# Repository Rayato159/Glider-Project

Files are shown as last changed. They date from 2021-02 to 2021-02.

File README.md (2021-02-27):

# Glider Project

 **Submitted by**
 1.	Ruangyot	Nanchiang	B6116736	(Project Manager)
 2.	Sahassawat	Rattanamongkolkul	B6113056	(CAD)
 3.	Kamonlaphat	Sitthitharanon	B6130268	(Documentation)
 4.	Apisit	Butprom	B6005375	(Manufacture)
 5.	Kobsiri	Seedakaew	B6007874	(Manufacture)
 6.	Chonlatorn	Sawangjit	B6007836	(Manufacture)
 
Present to Dr. Atthaphon Ariyarit.  
Semester 2-2563  
Suranaree University of Technology 

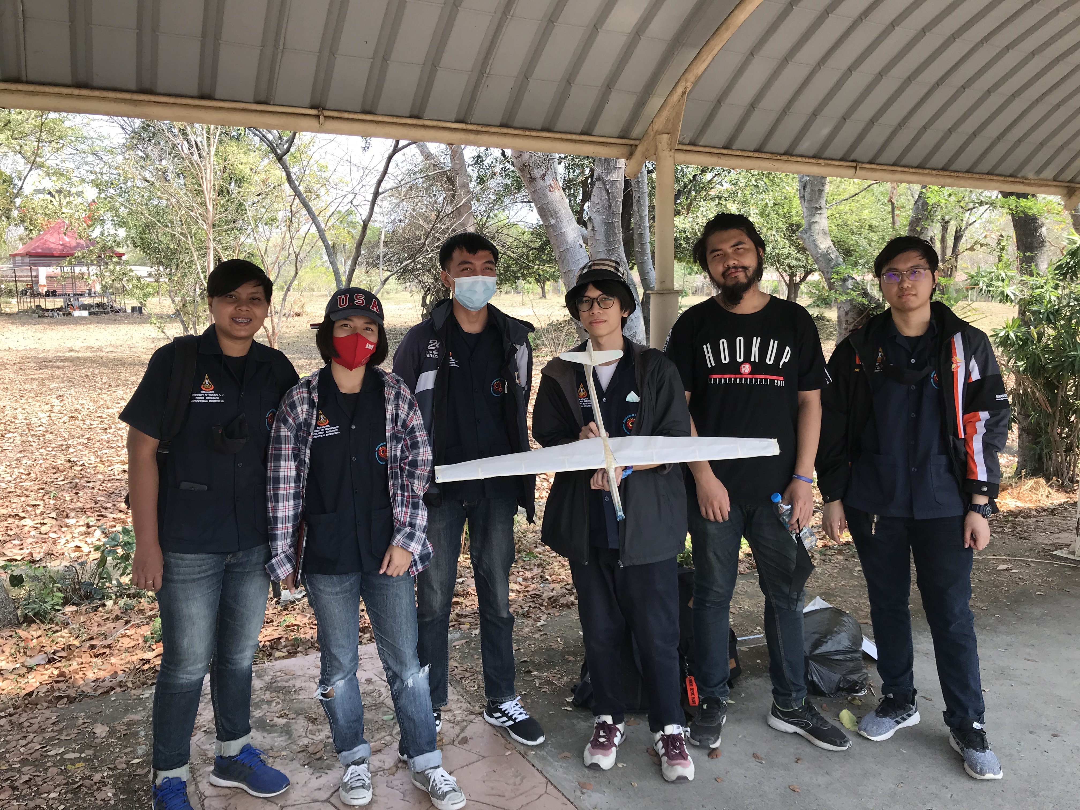
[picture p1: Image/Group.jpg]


This report is a part of the 537314 Flight Mechanics. The purpose of this report is to explain whole about of glider which we design whether why we need design like this.  
It’s just not only about to glider design but include manufacture, flight testing, inspection after flight testing and financial report.  
We describe step by step for who want to learn how to produce some small glider by our concept.  
This project is full of obstacles, because we just study the mechanics of flight and don’t know as much about aircraft design. Therefore, we used all the knowledge from aerodynamics and this subject by the full of power for produce the best glider as we can.  
Finally, If you read to this. We hope you to get the highest of knowledge by our report.  

Read more in full report.  
Flight Test: https://drive.google.com/drive/folders/1Cjw-I_sFbw1iagVFhjcJ2LFoMrj9WS8H?usp=sharing

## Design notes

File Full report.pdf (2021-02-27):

# Glider Project (Group No. 7)

537314 FLIGHT MECHANICS

### Submitted by

1. Ruangyot | Nanchiang | B6116736 (Project Manager)

### 2. Sahassawat Rattanamongkolkul B6113056 (CAD)

3. Kamonlaphat Sitthitharanon | B6130268 (Documentation)
4. Apisit | Butprom | B6005375 (Manufacture)
5. Kobsiri | Seedakaew | B6007874 (Manufacture)
6. Chonlatorn Sawangjit | B6007836 (Manufacture)
| | Present to

### Dr. Atthaphon Ariyarit

### Semester 2-2563

### Suranaree University of Technology

Preface
This report is a part of the 537314 Flight Mechanics. The purpose of this report is to explain whole about of glider which we design whether why we need design like this. It’s just not only about to glider design but include manufacture, flight testing, inspection after flight testing and financial report. We describe step by step for who want to learn how to produce some small glider by our concept.

This project is full of obstacles, because we just study the mechanics of flight and don’t know as much about aircraft design. Therefore, we used all the knowledge from aerodynamics and this subject by the full of power for produce the best glider as we can.

Finally, If you read to this. We hope you to get the highest of knowledge by our report.

Sincerely

project organizers

Contents

Glider Design Flowchart

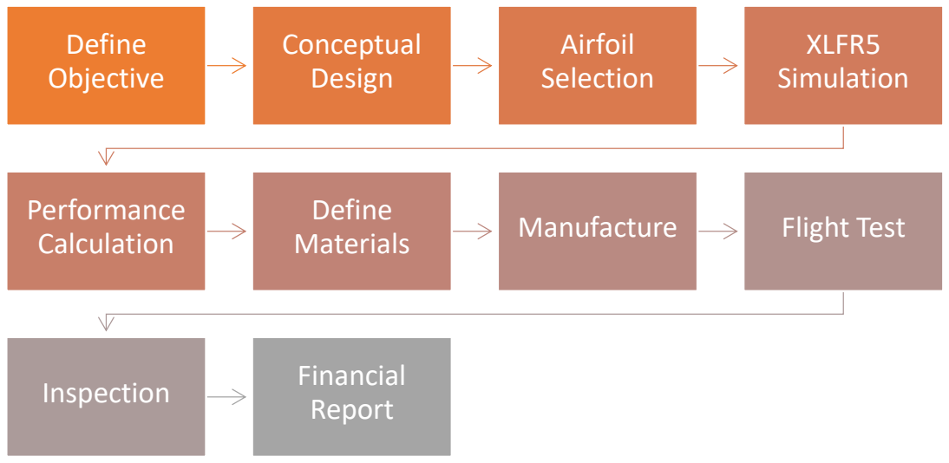
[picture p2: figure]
Define Objective; Conceptual Design; Airfoil Selection; XLFR5 Simulation; Performance Calculation; Define; Materials; Manufacture; Flight Test; Inspection; Financial; Report

Define Objective
1. Wingspan 1 m
2. Reynold number <= 400000 (Incompressible Flow)
3. Initial attitude 2 m
4. Longest range gliding
5. Low weight
6. High Cl/Cd and AR
7. High stiffness

Conceptual Design
The most important of glider is about to design for low weight, high Cl/Cd and AR, but in this project. We must design for high stiffness for structural test in another project.

First step. We need to define wing shape. From objective we need high Cl/Cd and AR then we define chord about 100 mm and we are all know as the best wing shape is elliptic wing (For lift produce on wing. Because elliptic wing has Oswald efficiency number = 1) But elliptic wing is hard to manufacture. Then taper wing is better to manufacture. Taper wing give speed more than rectangular wing for long range gliding. The good taper ratio are about 0.3 to 0.4. We choose taper ratio 0.4 and sweep angle 0 degree because is easy for manufacture. Then choose T tail for stable.

Next step. We used the RC plane calculator website to define all dimension and improve some dimension for suitability to structure.

Finally. We used Solidworks CAD software to design this glider, find center of gravity and calculate empty weight. Assume material to balsa wood.

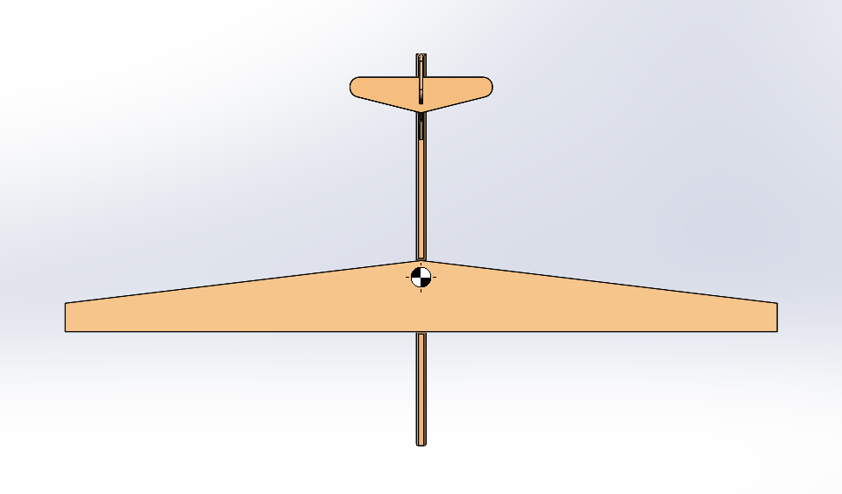
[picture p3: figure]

Figure 1 Top view

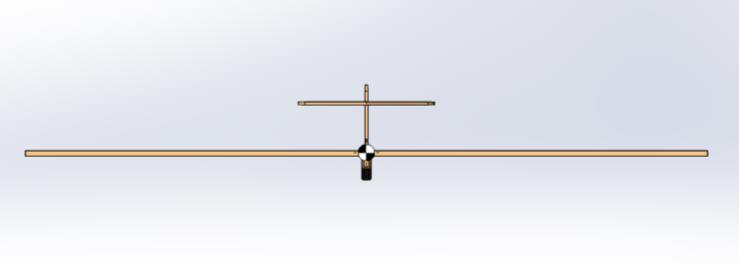
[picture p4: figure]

Figure 2 Front view

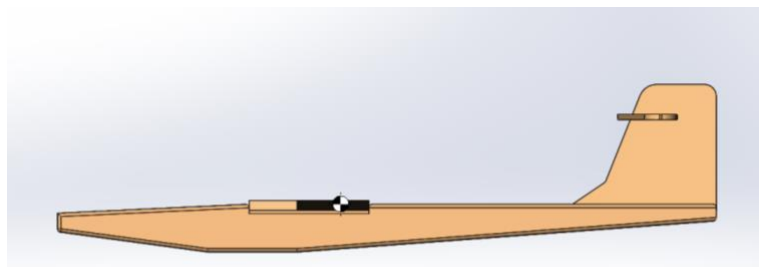
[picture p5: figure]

Figure 3 Right view

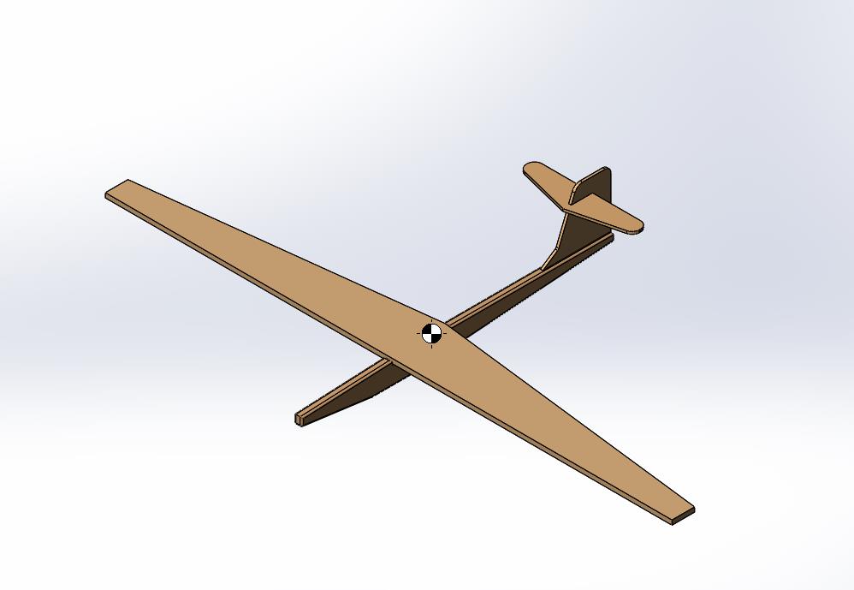
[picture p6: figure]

Figure 4 Isometric

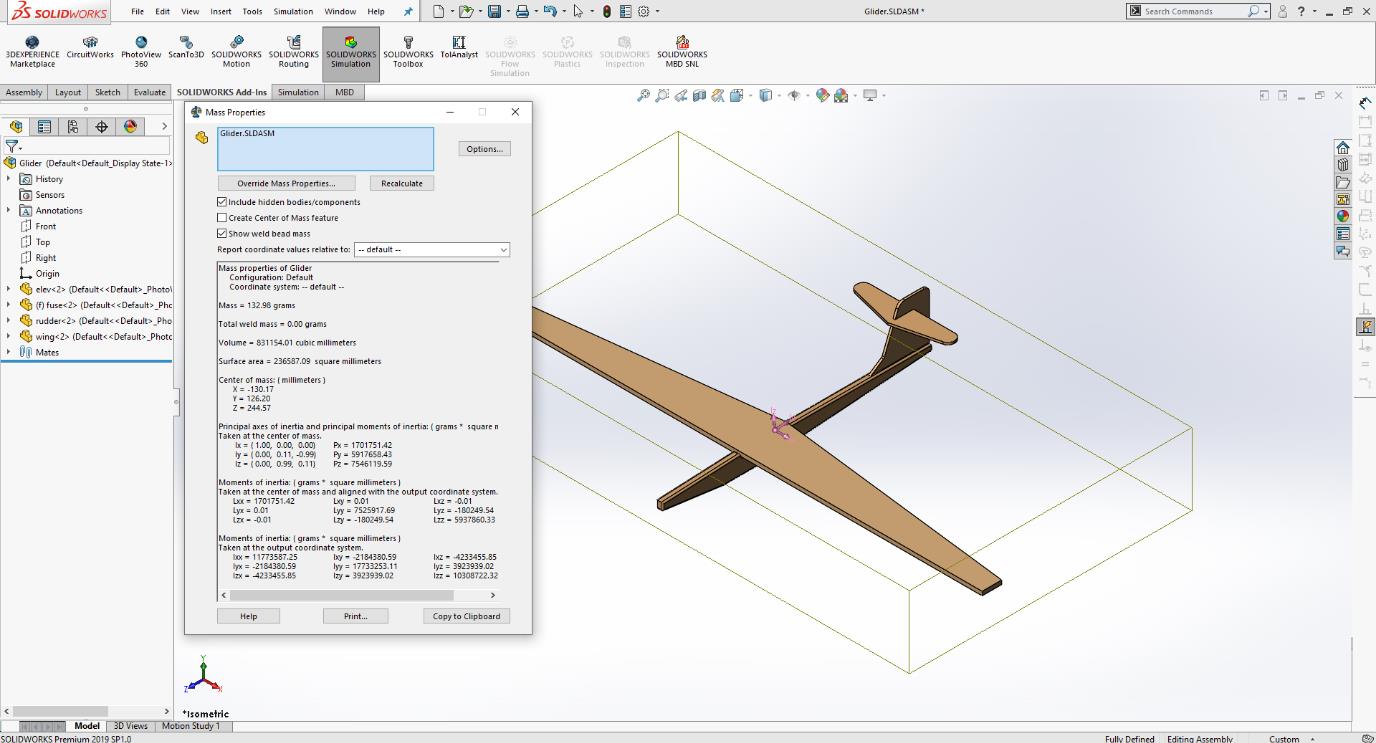
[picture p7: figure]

Figure 5 CG and mass calculation
Mass = 133 g; Center of Gravity (x, y, z) = (-130.17 mm, 126.20 mm, 244.57 mm);

Airfoils Selection
This step is also equally important, Because to improve Cl/Cd we need to meticulous with airfoil selection.

First step is about collection airfoils data. (We choose only NACA airfoils for standard) Go to “Airfoil Tools” website and collect all NACA airfoils coordinate point to JavaFoil. In JavaFoil set all

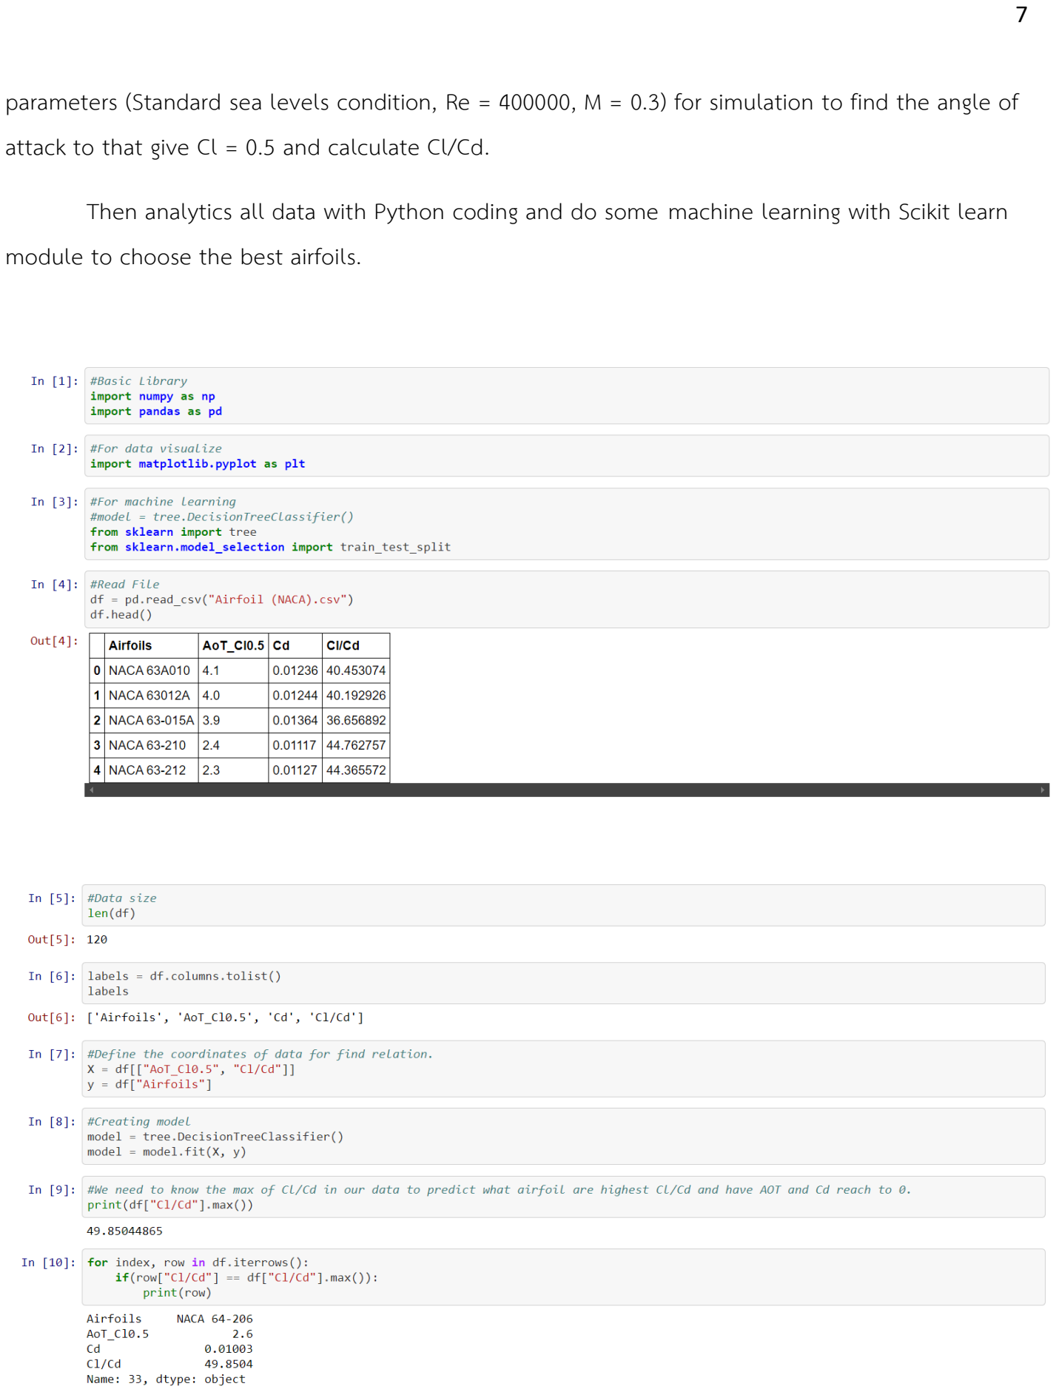
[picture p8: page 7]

parameters (Standard sea levels condition, Re = 400000, M = 0.3) for simulation to find the angle of attack to that give Cl = 0.5 and calculate Cl/Cd.

Then analytics all data with Python coding and do some machine learning with Scikit learn module to choose the best airfoils.

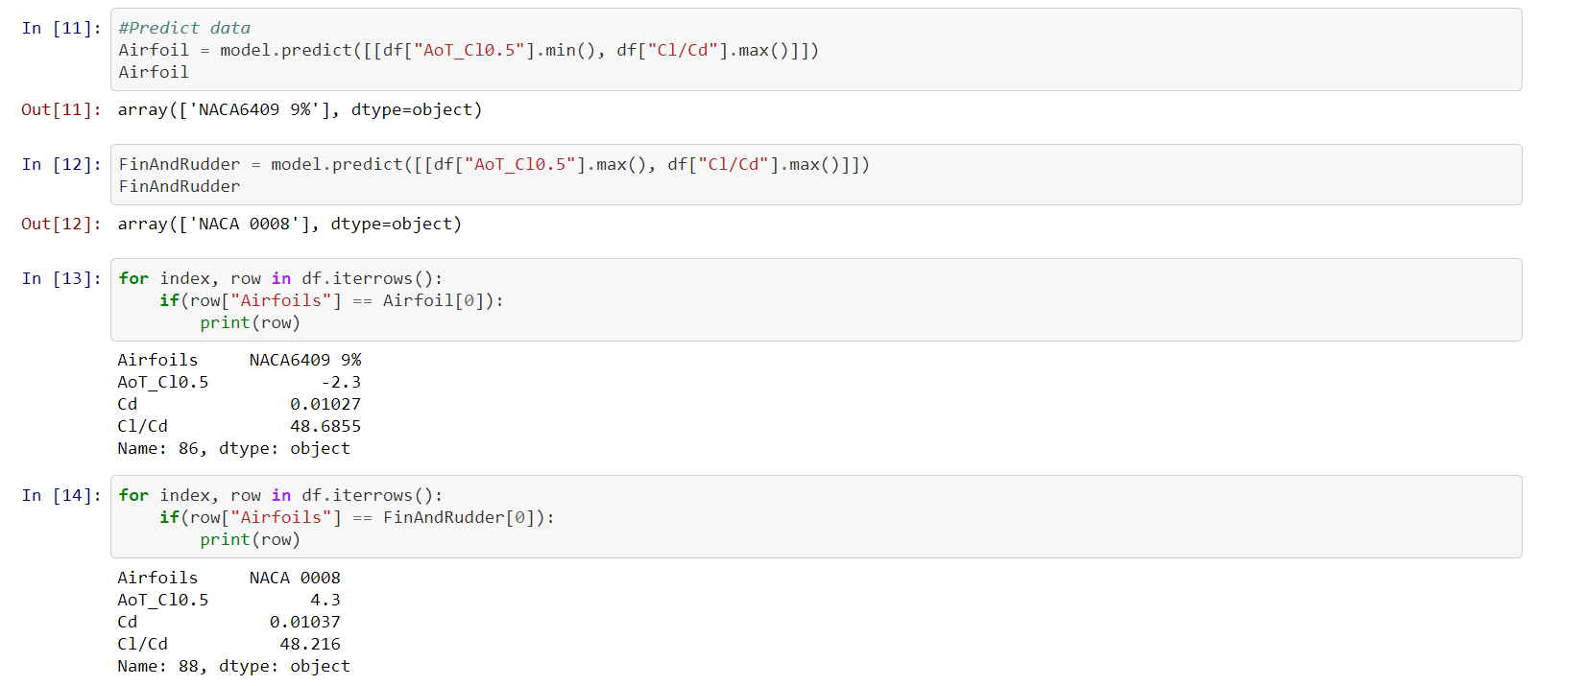
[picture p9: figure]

We used tree decision model because to define what if we need airfoil that have angle of attack and Cl/Cd by some value we expect. If wing we need lowest angle of attack and highest Cl/Cd for easy to launch the glider. If stabilizer we need symmetry airfoils and highest Cl/Cd for not disrupt the aerodynamics performance of the wing. what are airfoils we should get. And model score is 0.9833.

Thus, the result is NACA6409 for wing and NACA0008 for stabilizer (But used flat plate for tail because it’s can’t produce in reality for us).

XFLR5 Simulation
XFLR5 is free software and easy to use for RC plane simulation. This software can analysis airfoils and analysis RC plane. Then pull all information from conceptual design for define boundary conditions and get result below. Assume V = 9 m/s.

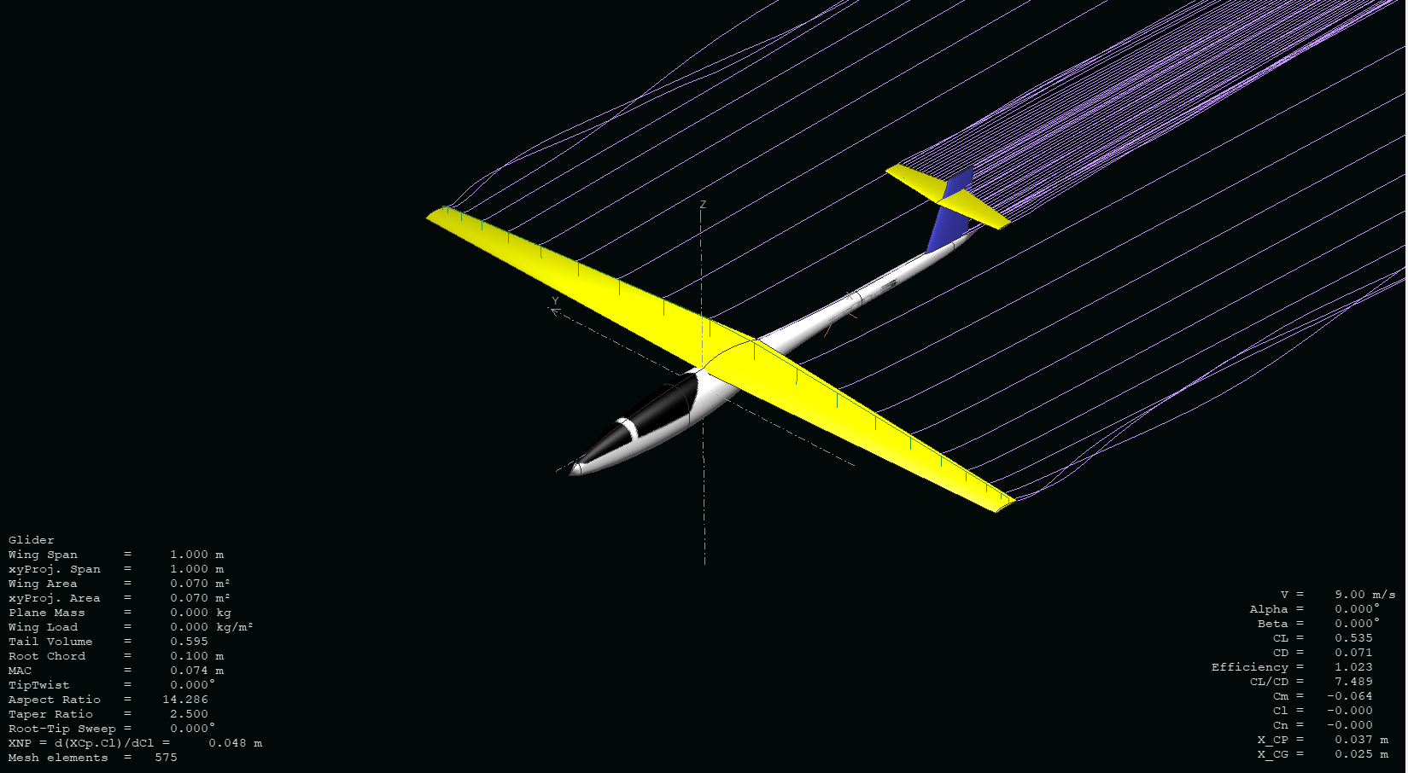
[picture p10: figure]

Figure 6 Streamline

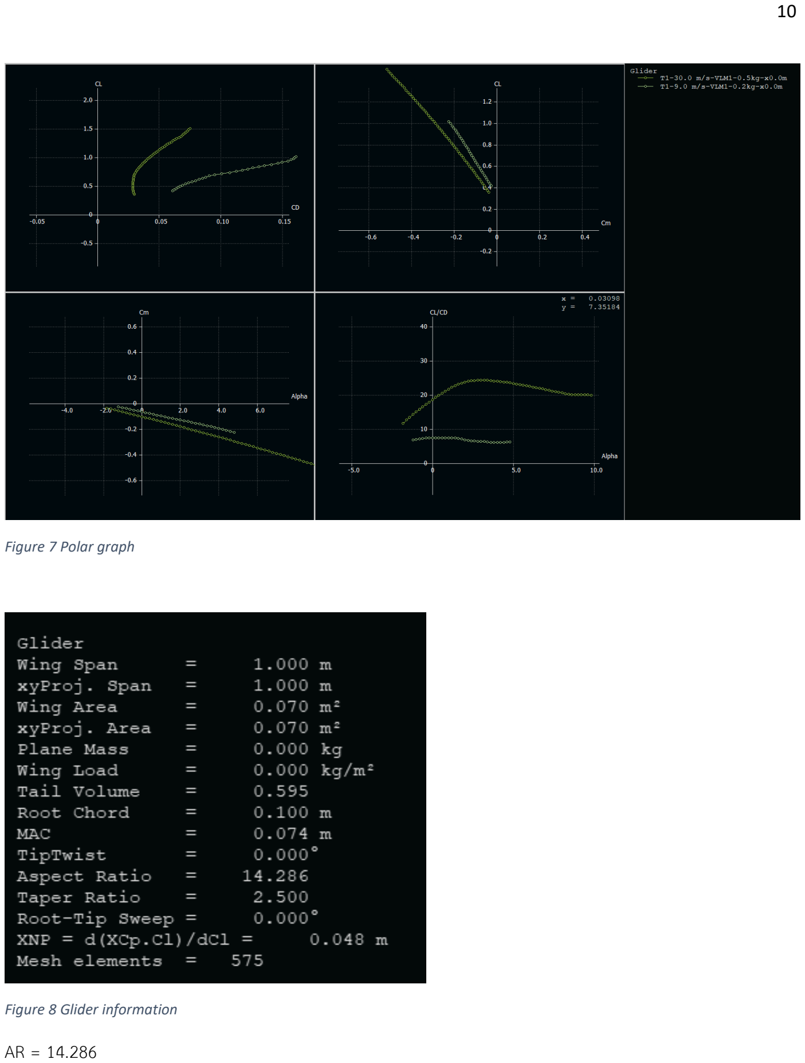
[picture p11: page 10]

Figure 7 Polar graph

Figure 8 Glider information
AR = 14.286

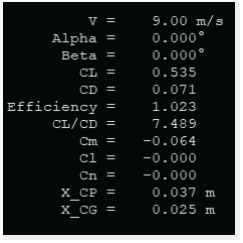
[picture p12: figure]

Figure 9 Glider performance
By plane analysis at angle of attack = 0 deg, Cl/Cd = 7.489, Cm = -0.064;

Performance Calculation
Consider an airplane in power off flight. The force acting on glider are lift, drag and weight. Thrust is zero because power off glider. Assume glider is constant velocity and flight path is horizontal parallel with ground. (L = W; T = D;)

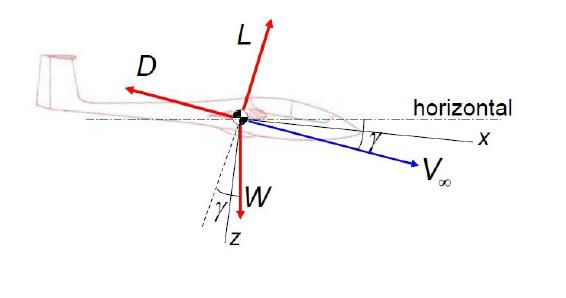
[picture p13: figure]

By the free body diagram is clearly whether if less of theta then range of glider will increase. If we want to know how far of glider can gliding. By following.

tan γ =

1
Cl
Cd

From that formula. Calculate gliding distance.

Cl
Cd = Glide Ratio = 7.489

tan γ =

1
7.489 = 0.134

Maximum range. h = 2 m

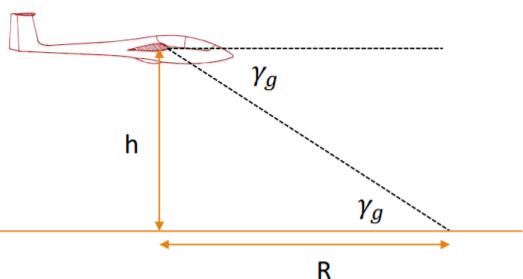
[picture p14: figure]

R =

h
tan γ

=

2
0.134 = 14.925 m

γ = tan⁻¹
(0.134) = 7.63 deg

Sink rate.

Sink rate =

Air Speed
Glide Ratio =

9
7.489 = 1.2 m/s

Endurance.

E =

h
Sink rate

=

2
1.2

= 1.67 sec

Thrust required.

TR =

W
Cl
Cd

=

0.133 ∗ 9.81
0.134 = 9.74 N ≈ 1 kg

Define Materials
At the first on conceptual Design. We assume all aircraft is filled by Balsa wood because Balsa wood is easy for manufacture, low cost and low weight. But in reality we can’t do that because we need to care about structure. Then we need to do some composite materials for more stiffness. And finally following the table below.
Materials | Part
Balsa Wood + PE Foam | Fuselage and Stabilizer
Balsa wood + Carbon Fiber | Wings
Kite Paper 50 gram | Wings Skin

***Carbon fiber spar has low weight and can improve stiffness for wings in vertical and axial load.

Manufacture
This process is full of obstacles. Because We have tools and resources in finite. We need to take carefully when we do all the parts by part of aircraft. We do “Handmade Workshop”.

Step by step

1. Fuselage: Cut the balsa wood and PE foam then stick together then fillet.
2. Stabilizer: Cut PE foam for 2 pieces first is vertical stabilizer second is horizontal stabilizer. Then cut some stick of balsa wood and stick together finally stick all to fuselage.
3. Airfoils: Cut come balsa wood and rasp to airfoils shape we select in first (7 pieces).
4. Wings: Used 2 carbon stick for wings spar and stick together with airfoils the cut some balsa wood to do bones of wings.
5. Wings Skin: Attach kite paper to wings.
6. Finally Step: Attach wing with fuselage by tape.

To more clarify whether how to manufacture.

Tools | Materials
Cutter | Balsa Wood, PE Foam
Rasp | Balsa Wood, PE Foam

Tools | Manufacture
Glue | Stick all the materials together
Tape | Attach wings to fuselage
Plasticine | Attach to glider for more weight and balance
Measured Tools | Used when
Vernier Caliper | Measured thickness
T Ruler | Check vertical or horizontal
Tape measure | Measured long range
Scales | Measured weight

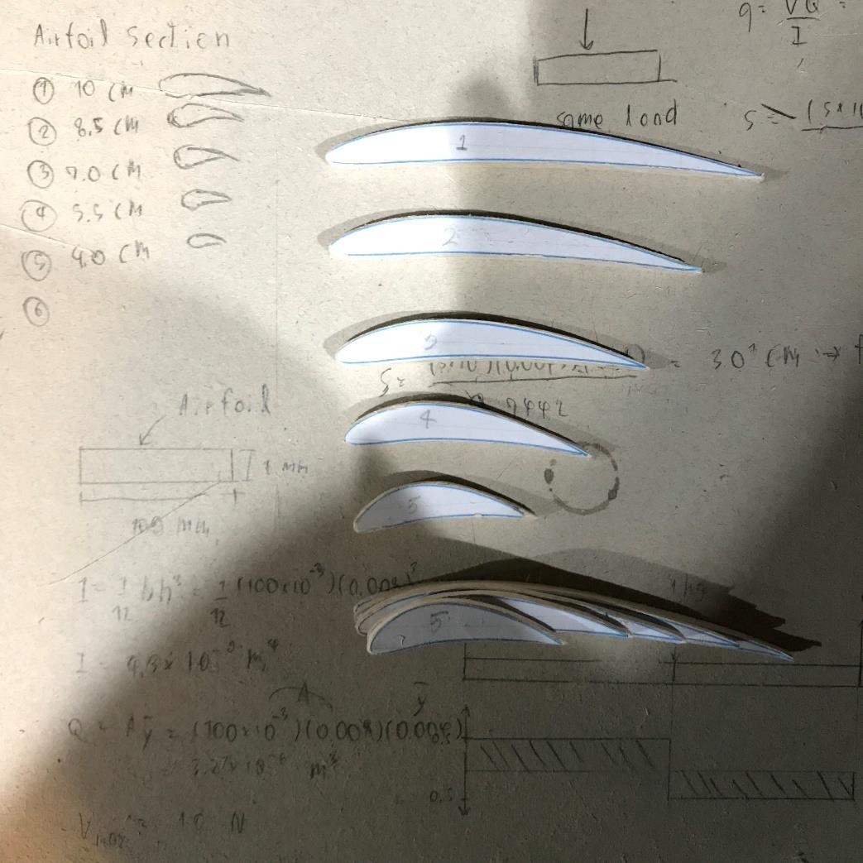
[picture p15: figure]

Figure 10 Airfoils NACA6409

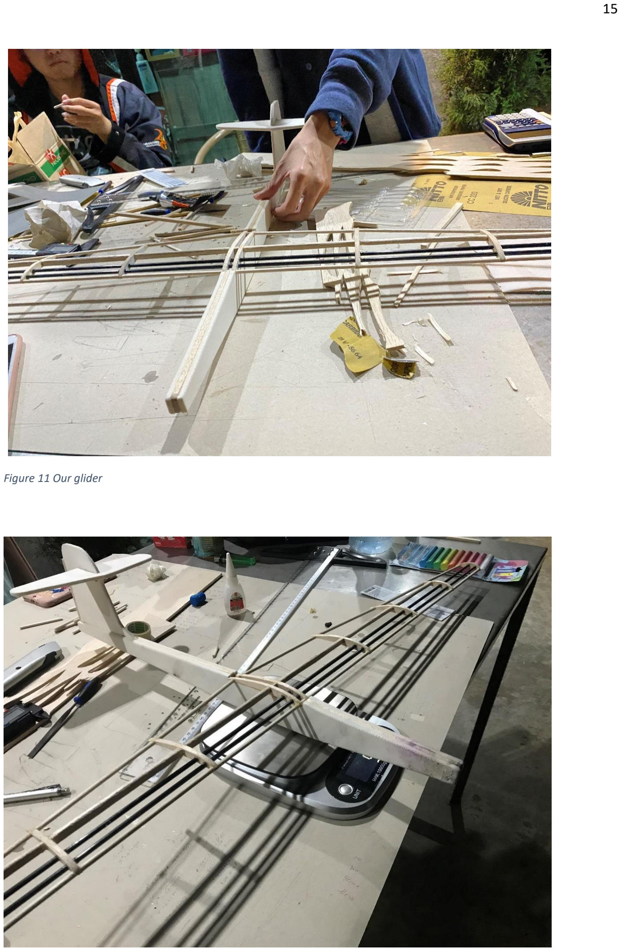
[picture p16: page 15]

Figure 11 Our glider

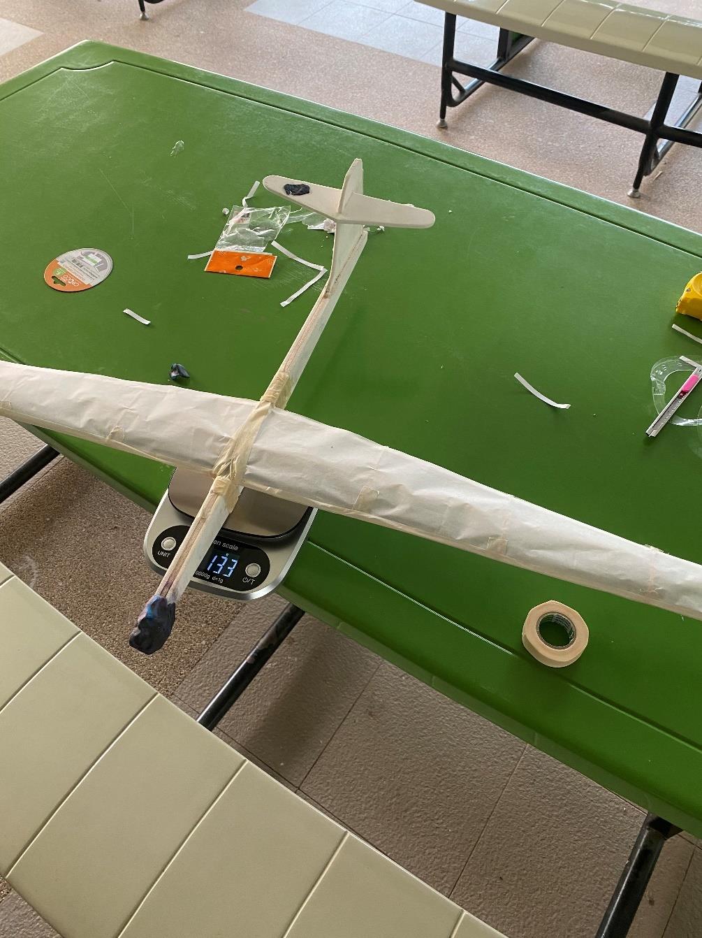
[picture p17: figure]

Figure 12 Finish

Flight Test
We took too many times for flight test and back to fix our glider. We do more and more to find the best result as expect. The link below is show some flight test.

Click here! (https://drive.google.com/drive/u/0/folders/1Cjw-I_sFbw1iagVFhjcJ2LFoMrj9WS8H)

Result on the real day test our glider can glide about 12.6 m error from theory by 16%.

Inspection
On the real test day our glider got some problem. There’s no stabilize because the last day before real flight got some damage with the trees too many times. Every time we fix we need to attach glue that will cause to no balance weight. Another problem is about stabilizer is not manufacture good enough.

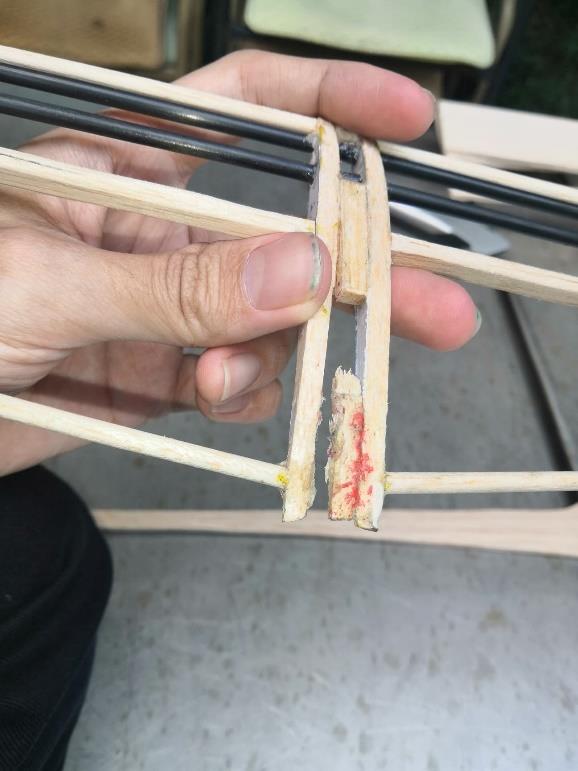
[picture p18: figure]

Figure 13 Damaged

Financial Report

Materials | qty. | price (Baht) | Total (Baht)
Balsa plate 100*1000*4 mm | 2 | 140 | 280
Balsa stick 4 mm | 4 | 20 | 80
PE Foam 500*500*4.5 mm | 4 | 75 | 300
Carbon Fiber Stick 4 mm | 2 | 120 | 240
Kite Paper 50 grams | 4 | 5 | 20
Nitto Tape | 2 | 27 | 54
Glue UHU | 1 | 75 | 75
Plasticine | 1 | 27 | 27
Sandpaper 220 | 1 | 13 | 13
Sandpaper 660 | 1 | 13 | 13
Sandpaper 1000 | 1 | 13 | 13
Rasp | 1 | 258 | 258
Total | | | 1373

Appendix

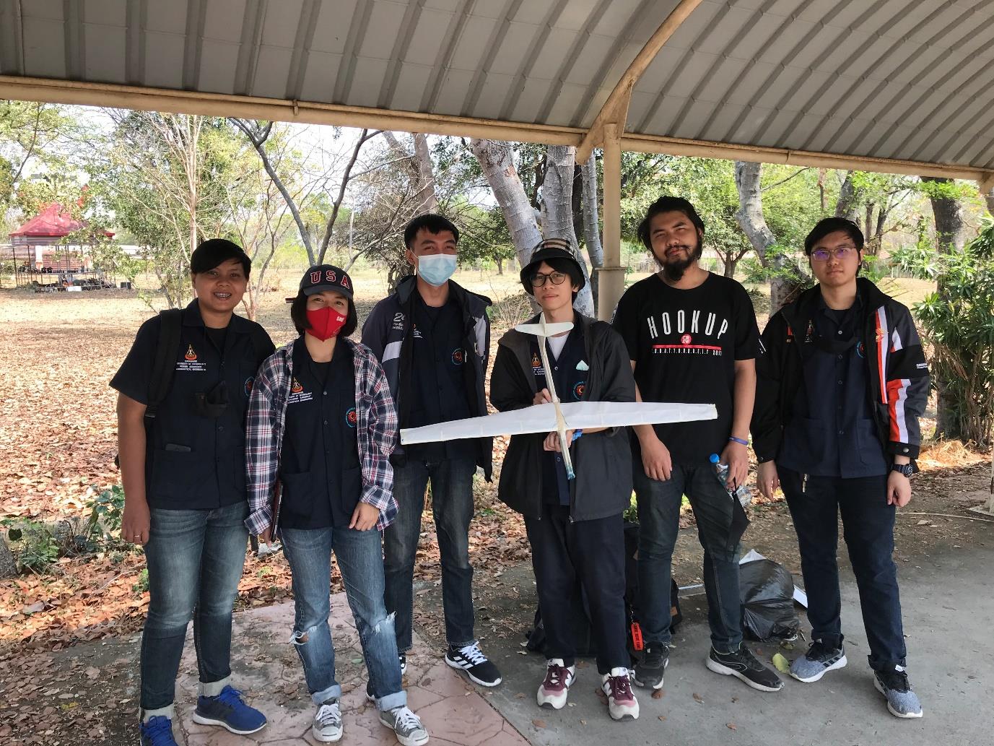
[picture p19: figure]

Figure 14 This is photo of our group after finish flight testing.

For more information about coding.

Github repository: https://github.com/Rayato159/Glider-Project

And finally, We need to say thanks to Mr. Sanya Phanprasert (He is our friend but not study with us.) for facilitate us to used workshop place and borrow tools to work.

References
1. John D. Anderson Jr. Introduction to Flight. 8

th ed. New York: McGraw-Hill. 2016
2. Federal Aviation Administration. Aerodynamics of flight. U.S. Department of Transportation. 2013
3. Andy Lennon. Basic of R/C MODEL AIRCRAFT DESIGN. Air Age Media Inc. 1996
4. Airfoils Tools. 2021; Available from http://airfoiltools.com/
5. Radio Control Info. 2021. Available from https://www.radiocontrolinfo.com/

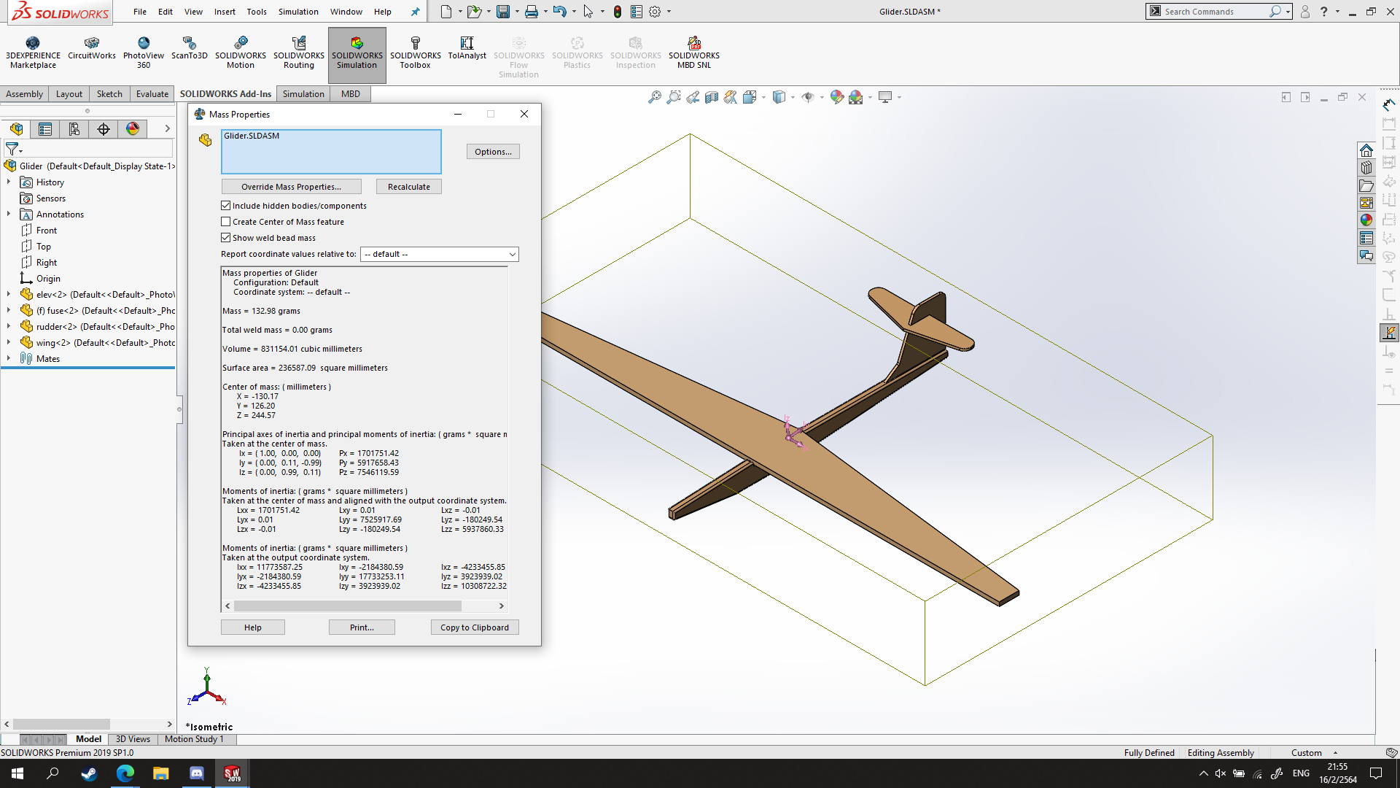
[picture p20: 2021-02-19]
Image/CAD.png

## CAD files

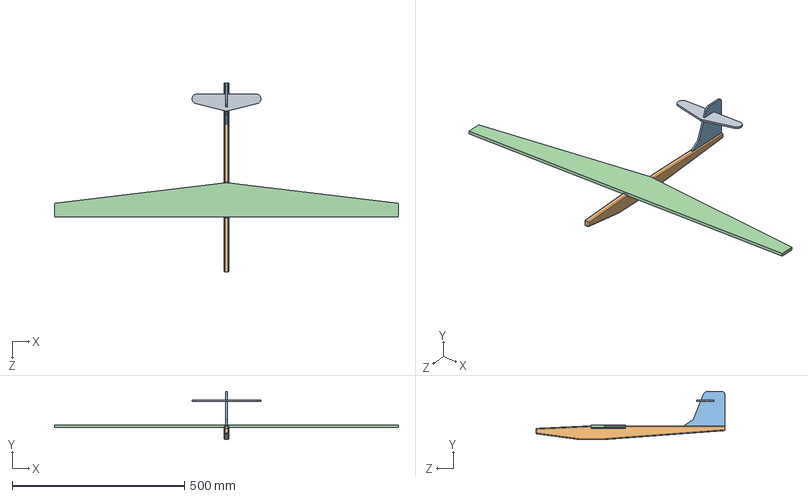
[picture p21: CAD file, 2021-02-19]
CAD Design/Glider.SLDASM
1000.0 x 140.0 x 550.0 mm
elev
fuse
rudder
wing

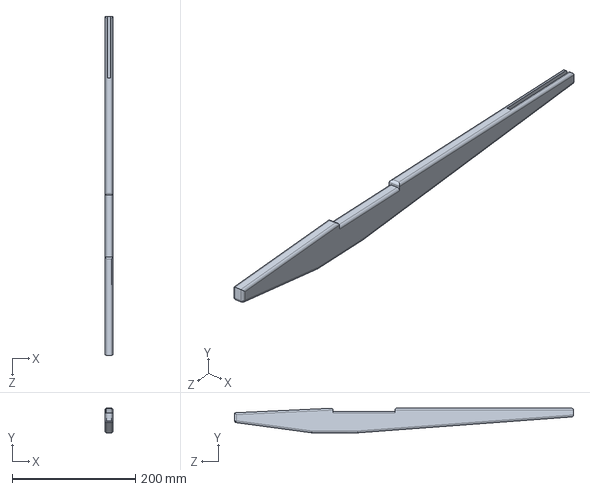
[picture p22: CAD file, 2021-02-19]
CAD Design/fuse.SLDPRT
13.5 x 40.0 x 550.0 mm

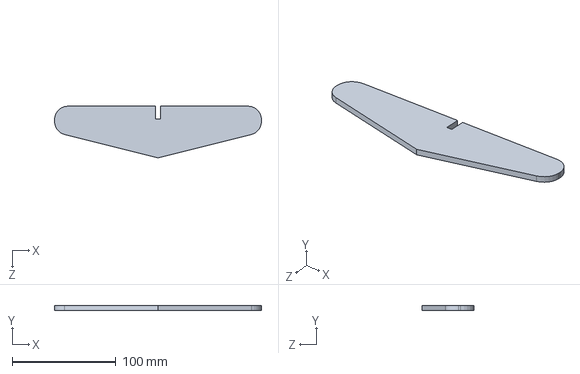
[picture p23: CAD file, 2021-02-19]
CAD Design/elev.SLDPRT
200.0 x 4.50 x 50.0 mm

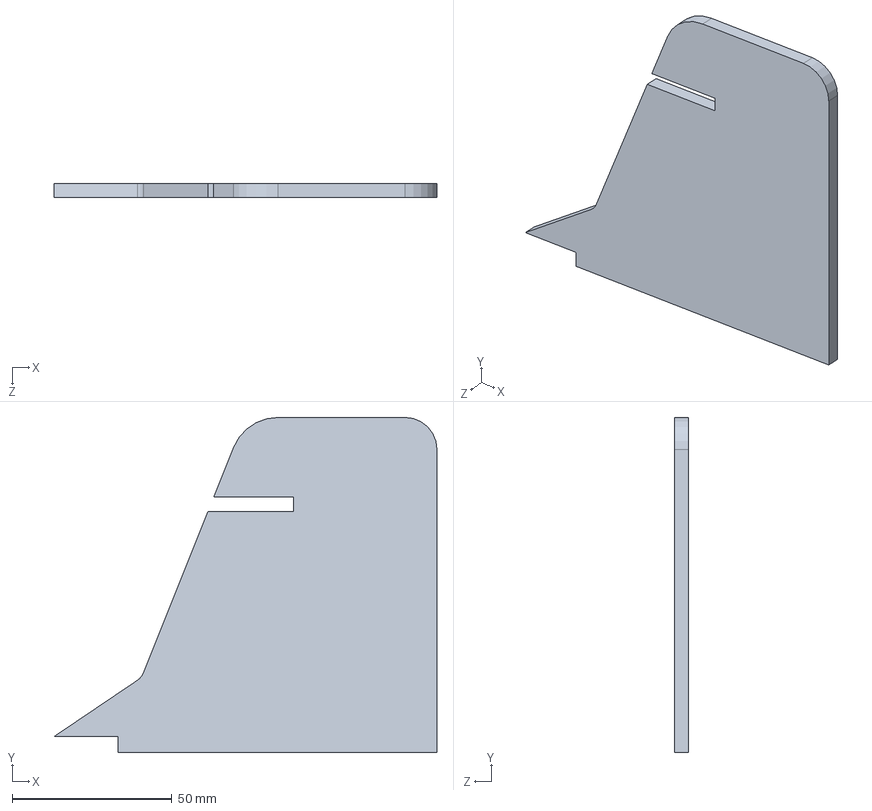
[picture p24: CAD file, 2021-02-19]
CAD Design/rudder.SLDPRT
120.0 x 105.0 x 4.50 mm

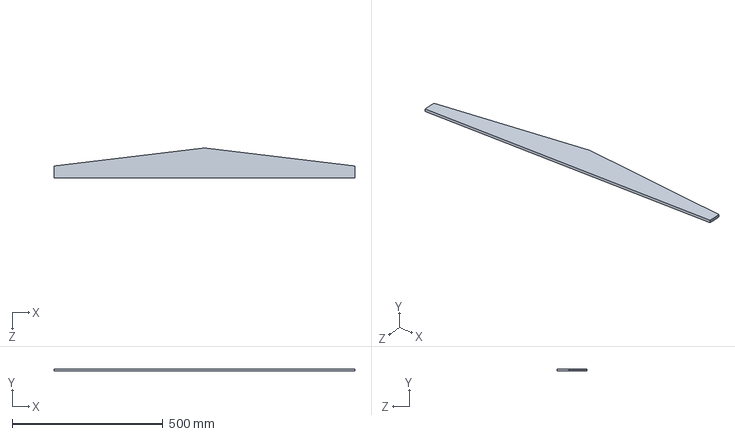
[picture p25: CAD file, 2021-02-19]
CAD Design/wing.SLDPRT
1000.0 x 8.00 x 100.0 mm

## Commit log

2021-02-07 Airfoil selection complete.
    Airfoils NACA 64-206
    AoF_Cl0.5 2.6
    Cd 0.01003
    Cl/Cd 49.8504
    [Airfoil (NACA).csv]
2021-02-10 Airfoil Part Complete
    [Airfoil (NACA).csv]
2021-02-19 Include CAD and Full report
    [Glider.SLDASM, elev.SLDPRT, fuse.SLDPRT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]
